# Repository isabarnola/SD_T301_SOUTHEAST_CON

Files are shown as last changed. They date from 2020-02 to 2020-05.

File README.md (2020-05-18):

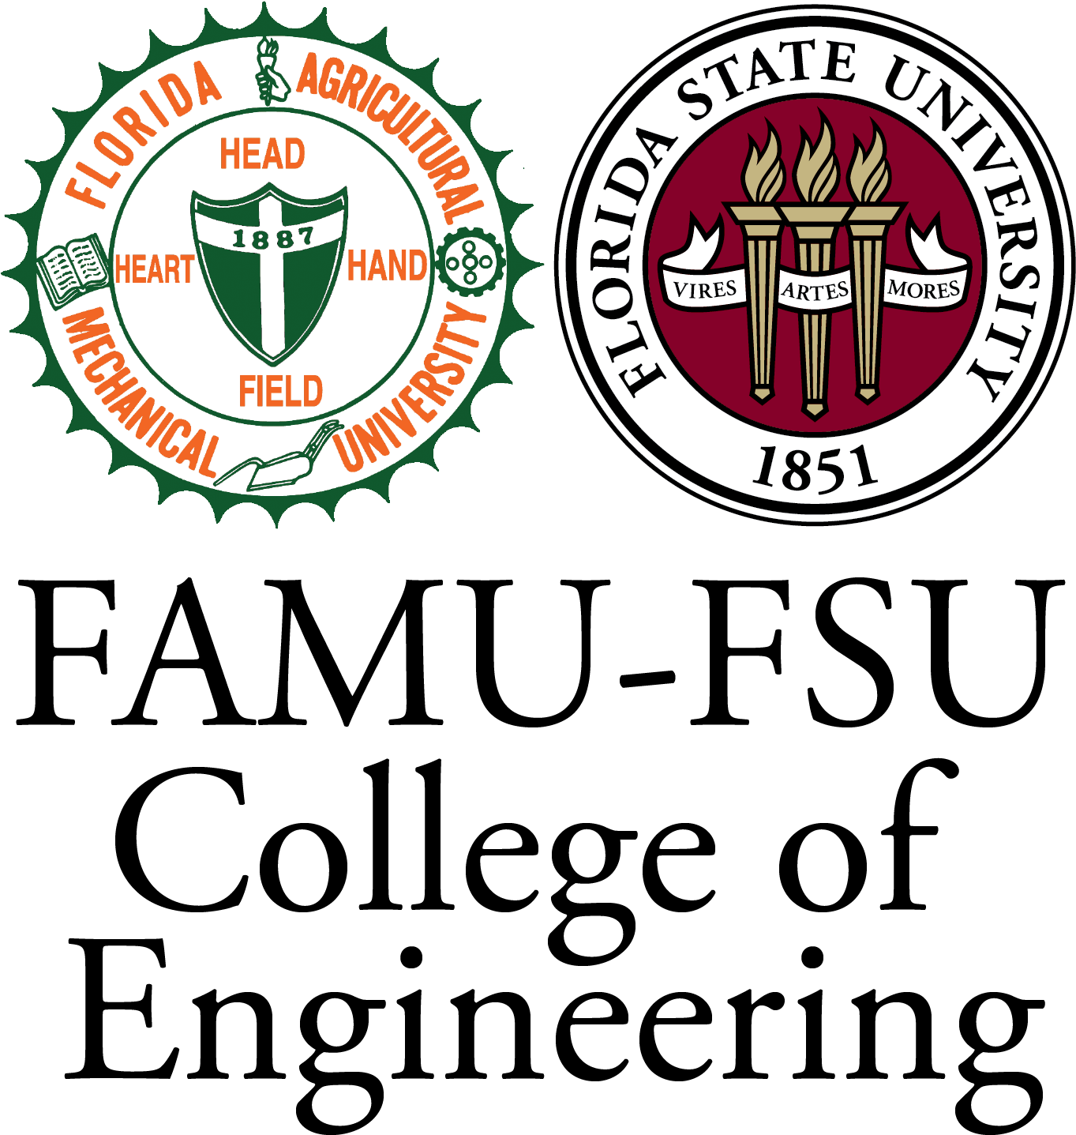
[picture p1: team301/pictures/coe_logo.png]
 

# FAMU-FSU Senior Design Team 301 : SouthEastCon Hardware Competition 

The IEEE SoutheastCon Student Hardware Competition is a yearly robotic design contest. 
This year’s game is to design an autonomous robot to do at least 1 of 2 tasks, within 3 minutes. 

Competition's webpage: 
```
https://attend.ieee.org/southeastcon-2020/student-program/student-hardware-competition/
```
Team's webpage:
```
https://ww2.eng.famu.fsu.edu/me/senior_design/2020/team301/
```
or
```
https://ww2.eng.famu.fsu.edu/~barnois/team301/
```

## 

Here you'll find the code for team 301's automated robot Ezio! As well as all other code related to the project.

### Ezio
Ezio is team 301 response to the souteascon harwarecompetition of 2020 1st challenge. He will stack from the bottom in a reverse PI Order.
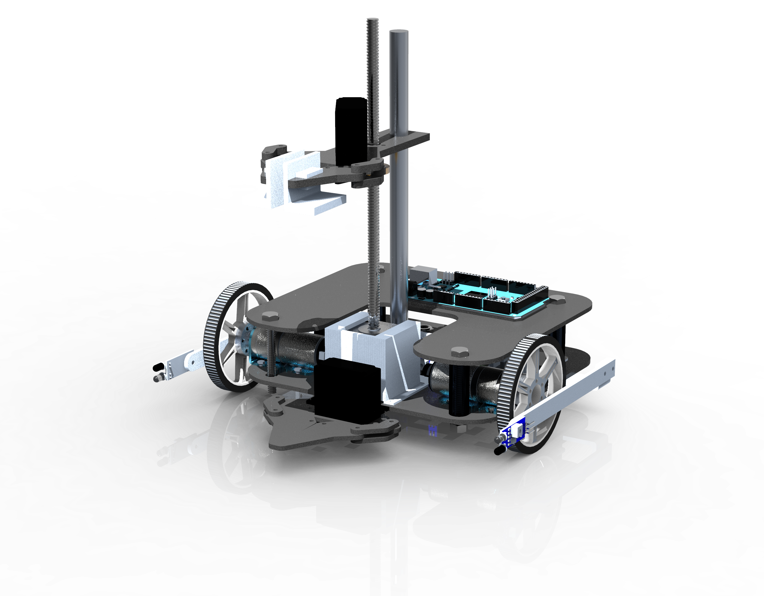
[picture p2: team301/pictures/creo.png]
Ezio


### Prerequisites

What things you need to install the software and how to install them

```
https://www.arduino.cc/en/Main/Software
```

### Software Overview

The software was designed to resemble a Finite State Machine. 
The tasks needed to do by Ezio were separated into modules, or states. 
Depending on the amount of blocks stacked, Ezio will use one state or another
in order to finish the task. Each state contains multiple functions in order 
to modularize the software's implementation. This type of desing allows 
for easier implemenation and testing as the project progresses.

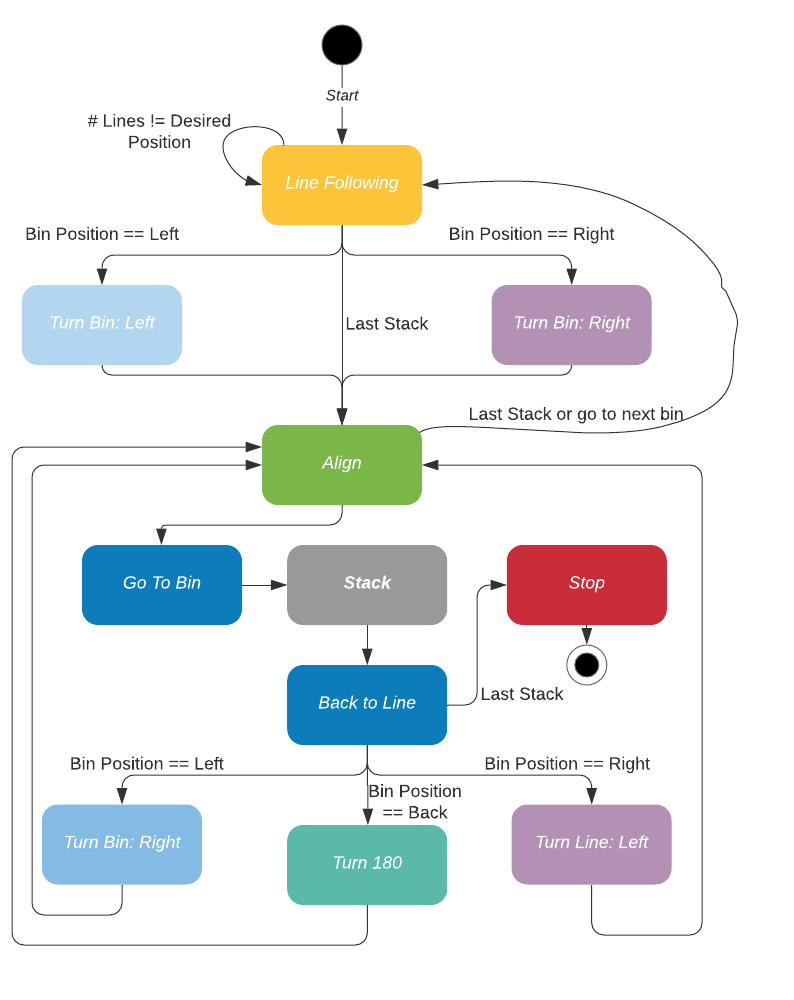
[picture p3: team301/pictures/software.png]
Software Diagram


## Authors

* **Isabel Barnola** - *Initial work* 

## License

No License

## Acknowledgments

* Hat tip to anyone whose code was used
* Inspiration
* etc

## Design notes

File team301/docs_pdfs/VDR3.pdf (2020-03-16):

# IEEE SoutheastCon Student Hardware Competition: Team 301

Isabel Barnola • David Bowen • Diego Campos • Alex Ndekeng • Abiel Souverain

Advisor: Dr. Bruce Harvey • Instructor: Dr. Jerris Hooker
Summary | Design

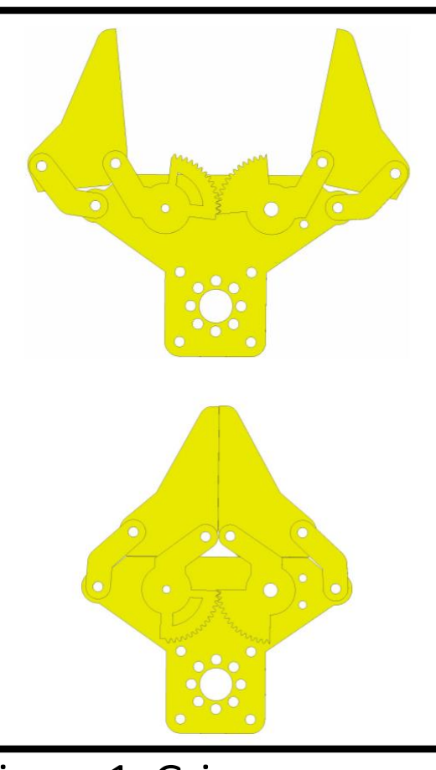
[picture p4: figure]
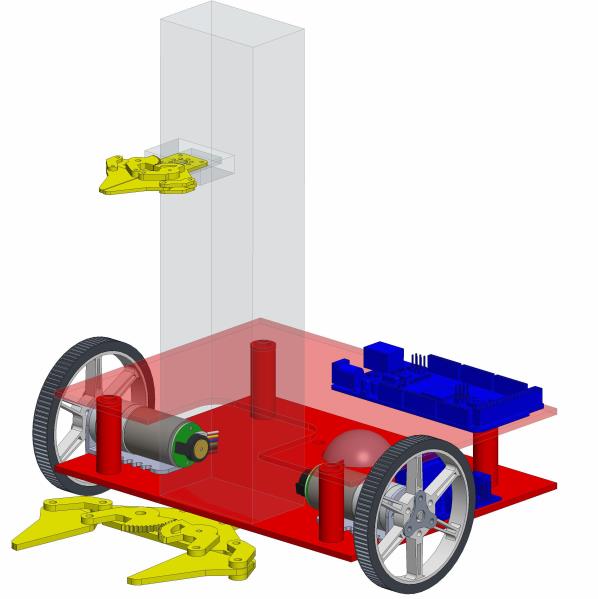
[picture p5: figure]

For the IEEE SoutheastCon 2020 Hardware Competition the goal is to make an automated robot that can complete at least one of the
challenges. Different points are awarded for different tasks, and the objective is to get the most points in 3 minutes.

There are two challenges, to stack Legos and push buttons. Each challenge is given points as shown in the figure below.
- Lego stacking: stack as many Legos in pi order where different colored Legos represent different numbers.
- Button pushing: push as many buttons in pi order where different buttons represent different numbers. Any additional button presses that are out of order will be added to the total, but this number is capped at 100.

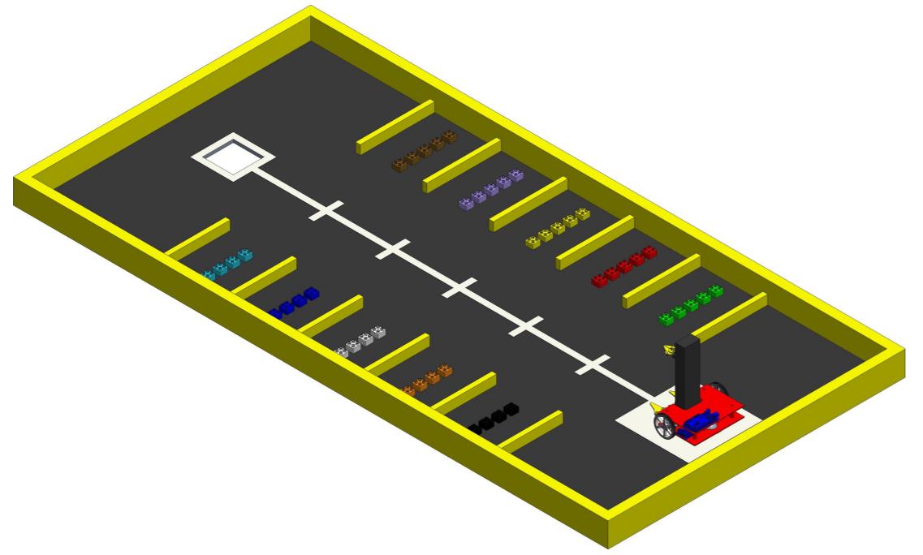
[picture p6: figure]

## Acknowledgements

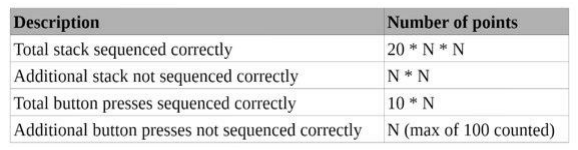
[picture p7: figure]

We thank Dr. Bruce Harvey for overseeing the design process, giving us access to a lab with many components that we will need, and for getting the competition play field built for us. We thank Dr. Hooker, Dr. Chuy, and Dr. McConomy for their constructive criticism in the design phase of our project.

## Challenges

## Future Work

Mechanical Design:
- Assemble prototype for initial testing
- Finalize design and dimensions Software Design:
- Navigational system
- Line following and line counting algorithm
- Stacking
- Elevator and gripper control
Electronic System:
- Assemble electronic components

## Development Tools

Software used:
- Arduino IDE – Microcontroller
- The automated system that governs the robot will be
deployed on an Arduino Mega.
- The system will be coded using C++
- CAD – Design
- Creo was the software used To develop the robot design

Figure 2. Robot Prototype

Figure 3. Robot in play arena

Figure 1. Gripper
opened/ Closed

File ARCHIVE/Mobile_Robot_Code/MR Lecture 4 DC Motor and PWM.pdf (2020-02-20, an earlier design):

## DC Motor and Pulse Width Modulation

Introduction to Mobile Robotics

1

DC Motor

§▪ Direct Current (DC) motor
- Converts electrical energy into rotational mechanical energy
- Earliest form of motor and it is easy to control.
- High torque and good speed controllability
- Typically used in robotic manipulators and mobile robots.
- Considered as torque generator

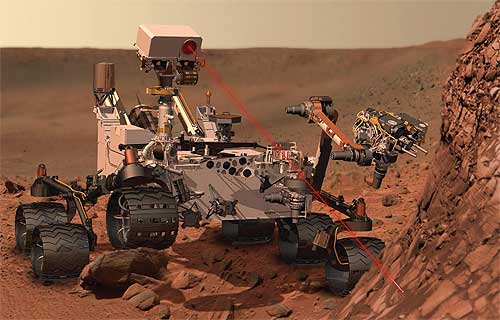
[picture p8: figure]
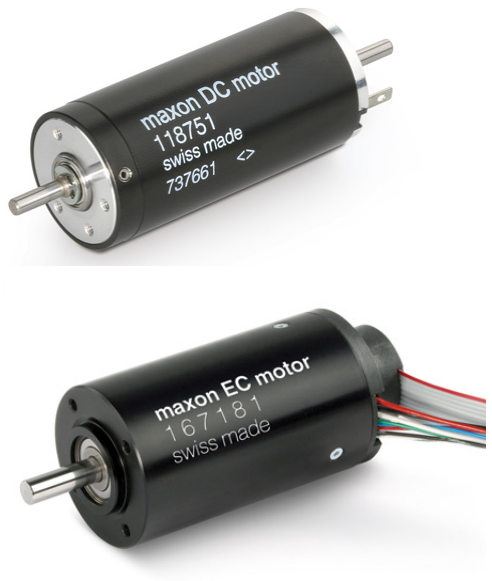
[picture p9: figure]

2

DC Motor

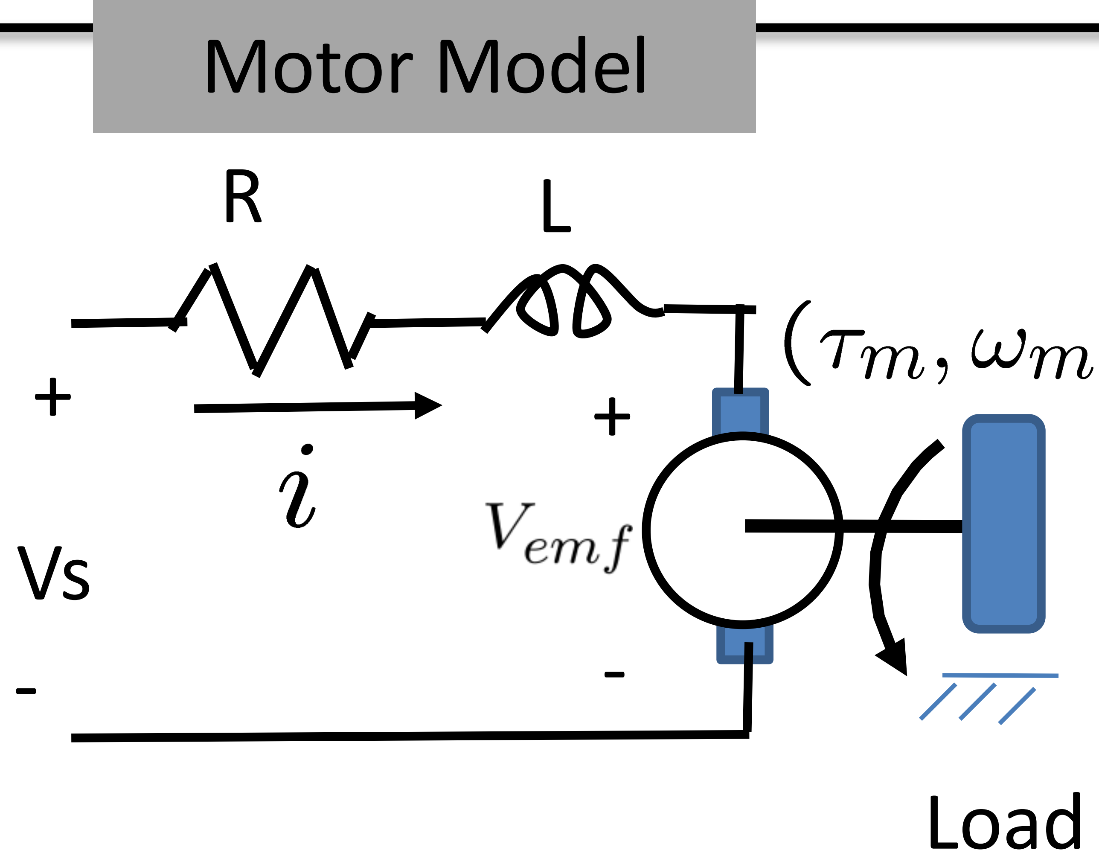
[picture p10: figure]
Load; Motor; Model

§▪ DC Motor Fundamentals
- current flowing through the motor is proportional to the generated torque
- angular rotation generates back-electromotive force
- operation:
- Vs is applied and
current is generated
which translates to
torque generation

3

R

armature

resistance
L

armature

inductance
Kv voltage

constant

V/rpm
Km

torque

constant

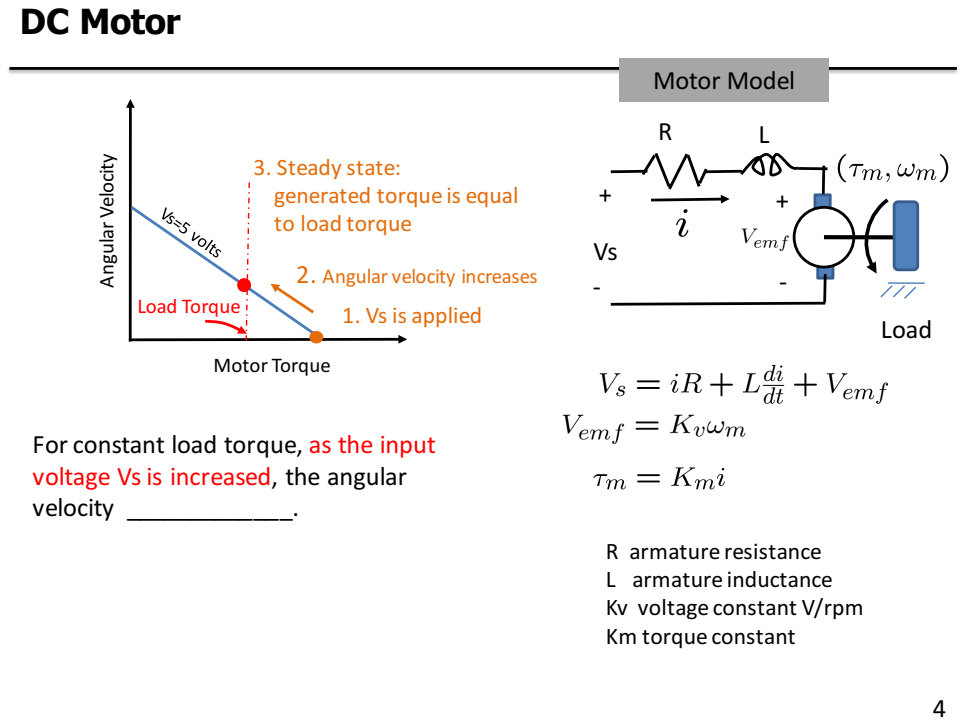
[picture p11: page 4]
DC Motor; Motor; Torque; Angular; Velocity; Load; For; constant; load; torque,; the; input; voltage; increased,; angular; velocity; armature; resistance; inductance; Kv voltage; V/rpm; torque; Model; applied; increases; Steady; state: generated; equal

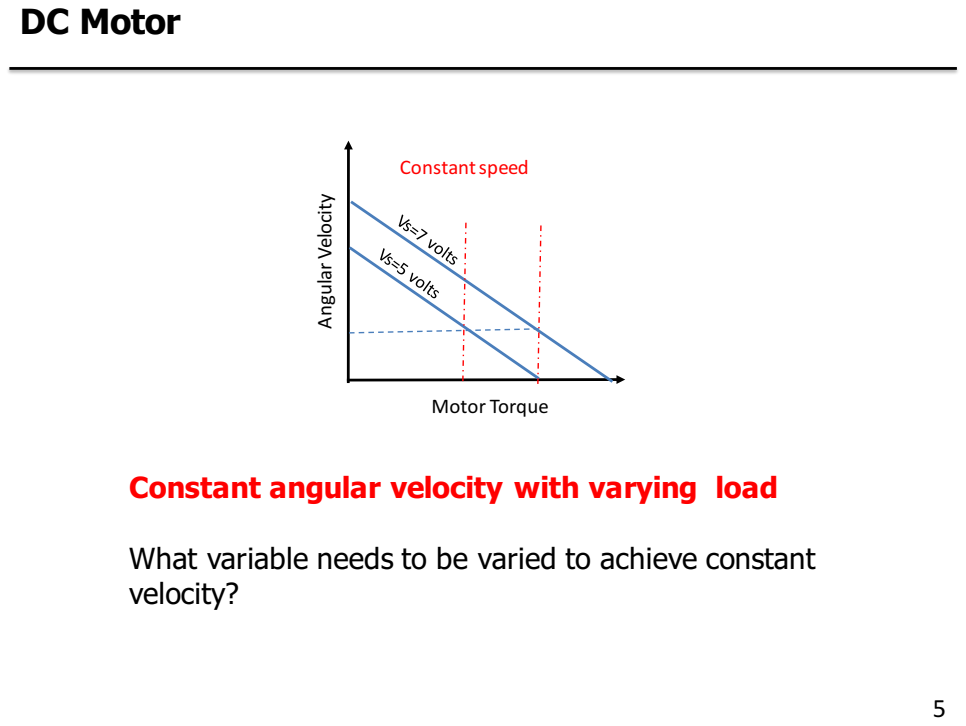
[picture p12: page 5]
DC Motor; Motor; Torque; Angular; Velocity; Constant; speed

Constant angular velocity with varying load

What variable needs to be varied to achieve constant
velocity?

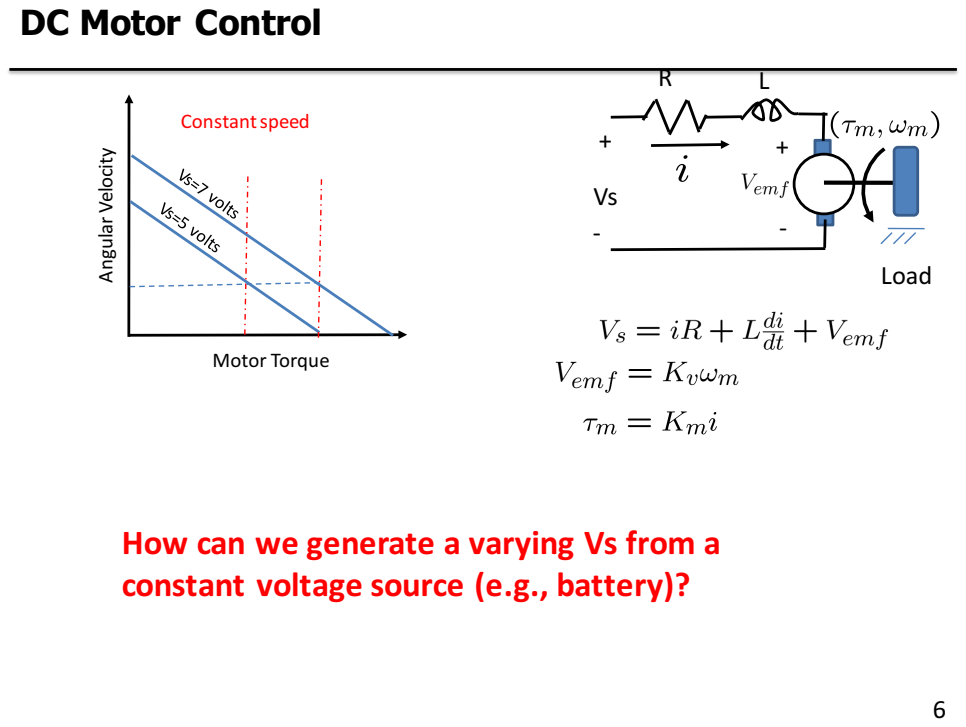
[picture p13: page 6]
Motor; Torque; Angular; Velocity; Constant; speed; Load; How; can; generate; varying; from; constant; voltage; source; battery)?

DC Motor Control

Introduction

§▪ Pulse Width Modulation
- an efficient way of controlling motors
- DC or average value is changed by varying the duty cycle

7

Introduction

§▪ Pulse Width Modulation
- Typical PWM freq. = 1/T is 100 Hz to 10 kHz.

8

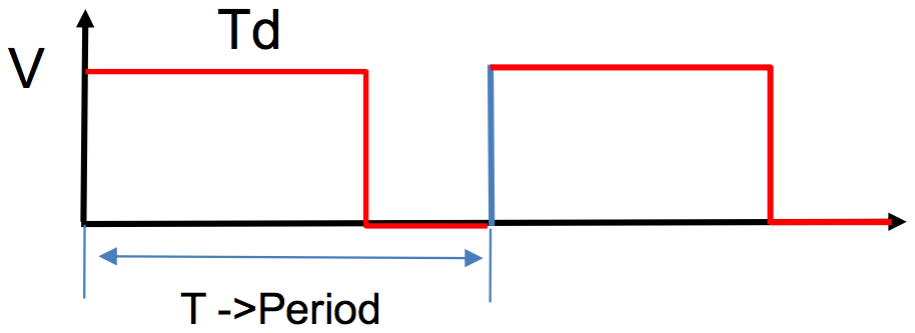
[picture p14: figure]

V"# =

$

% ∫ v(t) %
+ dt

V"# =

$
%

Area

PWM

§▪ Duty Cycle

9

Duty Cycle =

23456 75 8798 (:3;<)
26=7>: | x 100%

Duty Cycle =

?:
?

x 100%

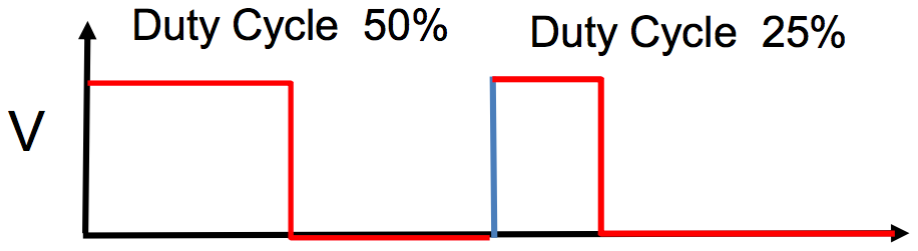
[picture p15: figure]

Pulse Width Modulation

§▪ Draw a PWM signal with 75% duty cycle

10

PWM and Microcontroller Bit Representation

§▪ Computer (Microcontroller)
- Arduino Mega 8 bit microcontroller will be used to control the mobile base

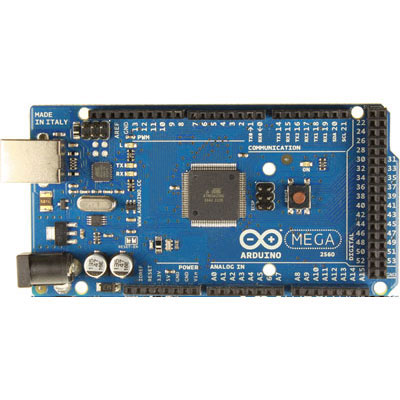
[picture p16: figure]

11

PWM and Microcontroller Bit Representation

§▪ BIT or bit
- smallest memory unit
§▪ N bit system (microcontroller)
- Represents N bit data size, register, data bus, and address bus.
- For example, an 8 bit system implies that the registers are 8 bit. §▪ N bit PWM
- Implies that 0--100% duty cycle is represented by 0 – (2A − 1).
- For example an 8 bit PWM has the mapping below
duty cycle (%)
0 | 0
50 | 127
100 | 255

12

PWM and Bit Representation

§▪ In terms of minimum change of output voltage (output voltage resolution), what does a high number of bits imply?

13

PWM on ATmega2560

§▪ Atmega2560 (Microcontroller)
- Used by Arduino Mega
- Note: Built in Arduino function for PWM has a frequency of 500 Hz, which is intended RC servo motors and other devices. Some applications require different freq. or higher frequency. Hence, we will not use Arduino built in function.

§▪ In the given sample code, PWM generation will be based on TIMER 5
- Pin 45 for motor 0
- Pin 46 for motor 1

14

PWM Implementation Using Arduino Mega

15

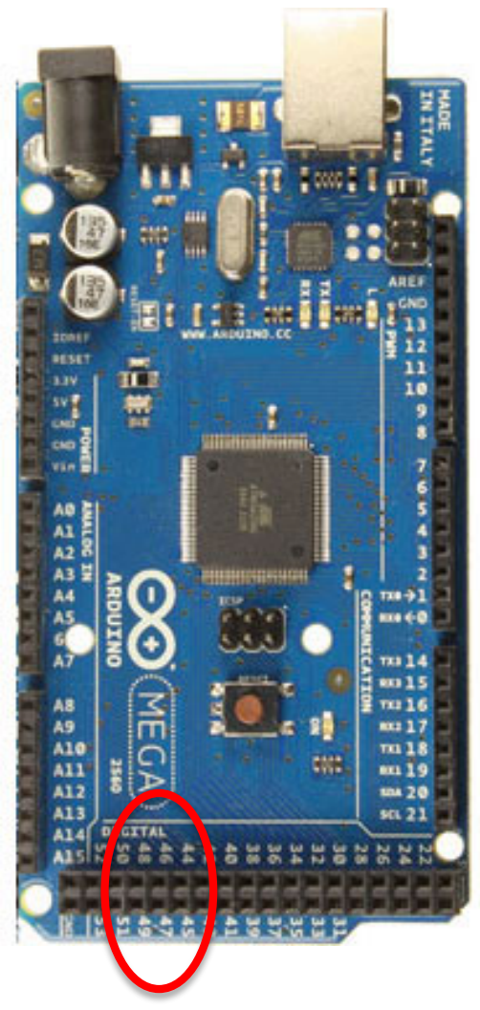
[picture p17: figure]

Code Initialization

16

pwm_init();

void pwm_init(void){
pinMode(45, OUTPUT);
pinMode(46, OUTPUT);
TCCR5A = _BV(COM5A1) | _BV(COM5B1) | _BV(WGM52) |
_BV(WGM50);
TCCR5B = _BV(CS51) | _BV(CS50); //set prescaler to 64
OCR5A = 0; OCR5B = 0;
}
The

above

code

(pwm_init)

initializes

timer

5

as

PWM

generators(2

PWMs).
The

PWMs

are

8

bits

at

500

Hz.

TCCR5A,

TCCR5B,

OCR5A,

and

OCR5B

are

microcontroller

registers

and

already
defined

in

the

ARDUINO

environment.

PWM Duty Cycle

§▪ OCR5A (Output Compare of TIMER 5)
- Will set the duty of channel/motor 0. The maximum value of duty is 255.
255 -> 100% duty cycle 127 -> 50% duty cycle
0 | -> | 0% duty cycle

17

PWM Duty Cycle

18

§▪ OCR5B
- Will set the duty of channel/motor 1. The maximum value of duty is 255.
255 -> 100% duty cycle 127 -> 50% duty cycle
0 | -> | 0% duty cycle

Motor Driver

19

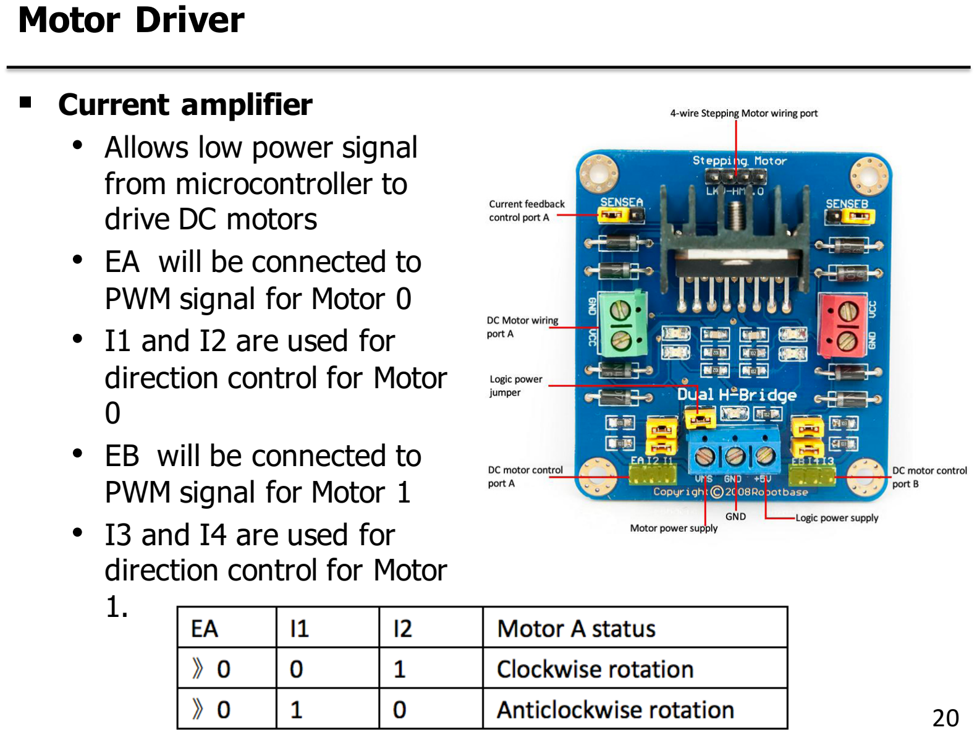
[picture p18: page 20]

Motor Driver §▪ Current amplifier • Allows low power signal

from microcontroller to
drive DC motors
- EA will be connected to PWM signal for Motor 0
- I1 and I2 are used for direction control for Motor 0
- EB will be connected to PWM signal for Motor

1
- I3 and I4 are used for direction control for Motor 1.

20

Motor Driver

§▪ Motor Control Summary
- Aside from PWM signal, a motor needs 2 digital pins for direction.
- For a differentially steered (2 wheels) mobile robot
- 2 motors – 2 PWM signals and 4 direction pins

21

Motor Functions

22

motor_init()

initializes

the

PWM

and

direction

pins

of

the

motors

set_motor_speed(channel,

speed

)
channel

=

0

implies

motor

0

and

channel

=

1

-‐>

motor

1
speed

=

127

implies

50%

duty

cycle

moving

forward
speed

=

-‐127

implies

50%

duty

cycle

moving

backward

void motor_init(void);

void set_motor_duty(int channel, int duty);

Trouble Shooting

set_motor_speed(0,100) should yield a forward motion. If it is backward, you can reverse the motor wiring (+ -> -) or change the direction code.

23

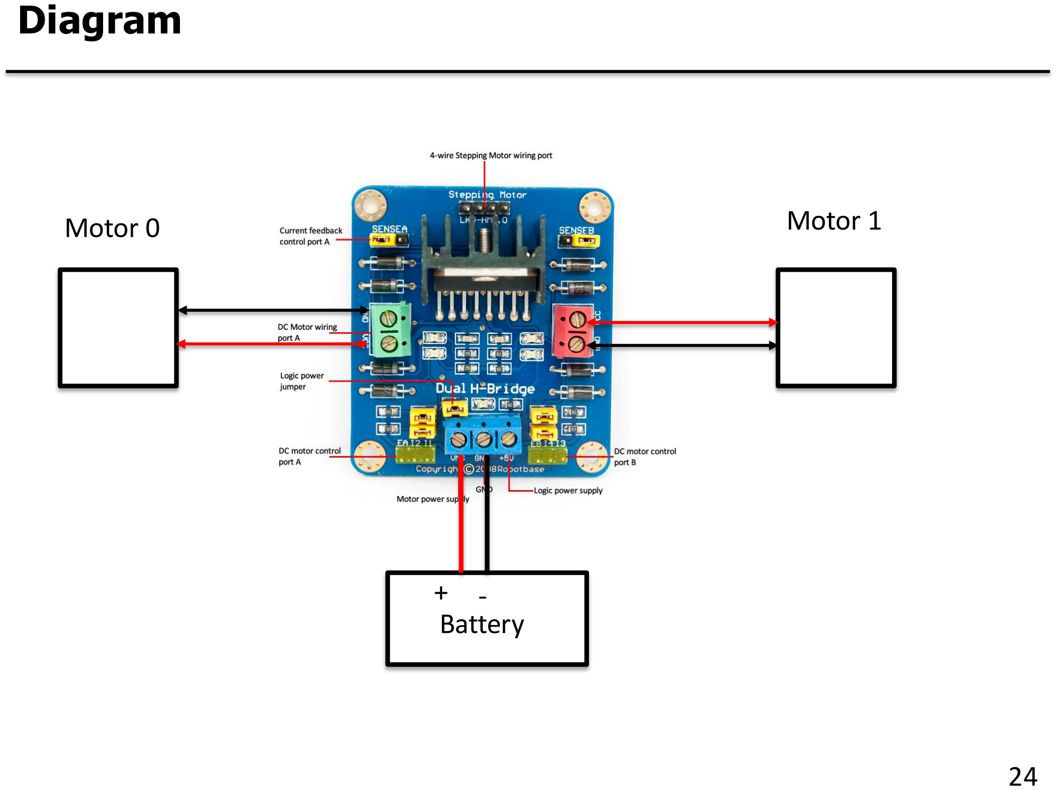
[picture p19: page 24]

Diagram

24

Motor

0 | Motor

1

+ -‐ Battery

Pins

25

Arduino | Motor Driver
45 | EA
50 | I1
51 | I2
46 | EB
52 | I3
53 | I4
GND | GND
+5V | +5V

PWM

PWM

Direction
Direction

Direction
Direction

Sample Code

26

#include "mrobot.h”

void setup()
{
motor_init();
}
void loop() {
set_motor_speed(0,100);
set_motor_speed(1,100);
}

Summary

- The provided motor functions can change the voltage and thereby change the speed of the motor.

- The main drawback is that the implementation is open loop, meaning for a constant duty or voltage, the speed will change if the load varies.

27

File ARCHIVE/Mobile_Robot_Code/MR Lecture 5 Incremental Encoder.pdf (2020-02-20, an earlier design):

## Mobile Robot: Measuring Wheel Position Using Incremental Encoder

1

Introduction

§▪ Incremental Encoder
- Use to measure angular position and generally attached to motor shaft.

2

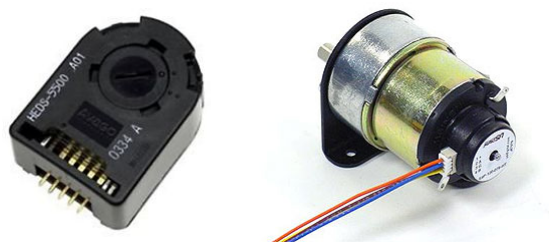
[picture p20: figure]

Introduction

§▪ Incremental Encoder
- Generates two signals that are 90 deg. out of phase

3

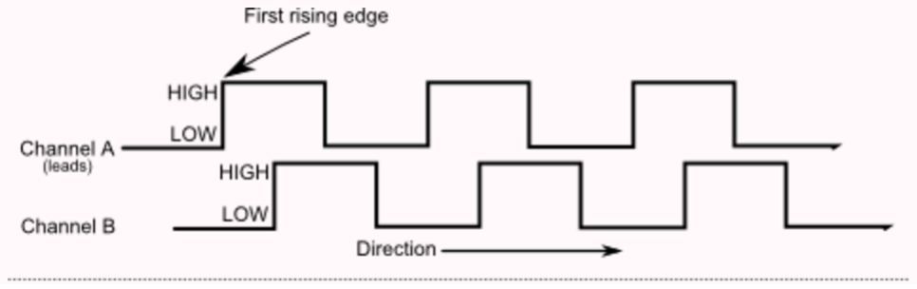
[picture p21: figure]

Introduction

§▪ Decoding Incremental Encoder (Quadrature Decoding)
- Channel A and Channel B will be wired to interrupt pins. If there is a change in state for example high to low or low to high an interrupt is triggered.
- Quadrature decoding – all rising and falling edges create interrupts. Quadrature since there are four sign changes in Ch A and Ch B for one encoder count.

4

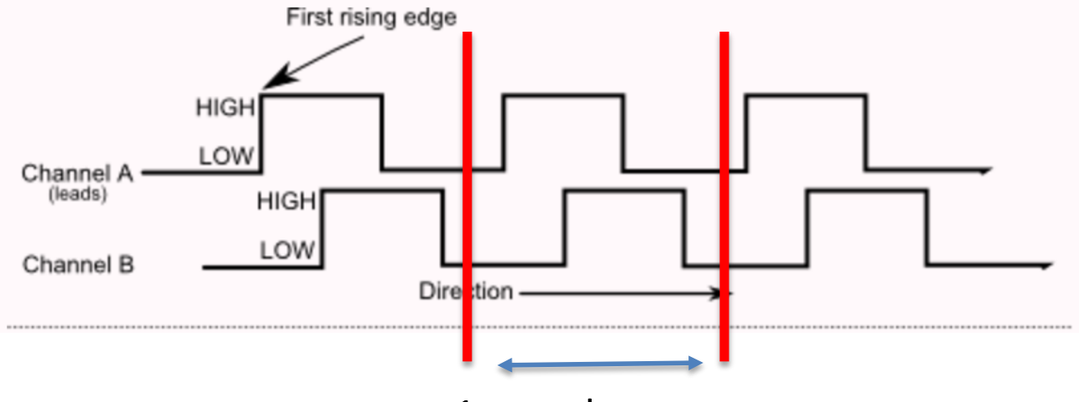
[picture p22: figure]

1

encoder

count

Introduction

§▪ Decoding Incremental Encoder (Quadrature Decoding)
- State assignment – assign states to one count as basis for determining direction.

5

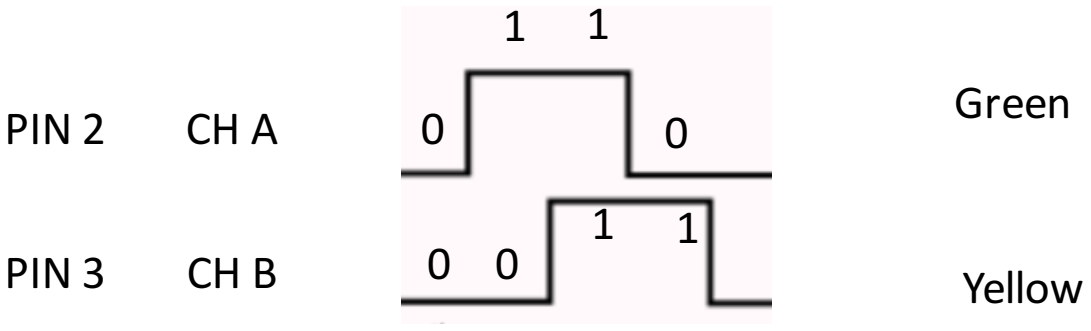
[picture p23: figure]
PIN; Yellow; Green

CHB

CH

A
0
0 | 0
1 | 1 1 | 1 0

State

0 | 1 | 3 | 2

Decoding

§▪ Conditions:
- If current state is 0 and next state is 1 then in clockwise direction (increment the value of the encoder)
- If current state is 0 and next state is 2 then in counter clockwise direction (decrement the value of the encoder)

6

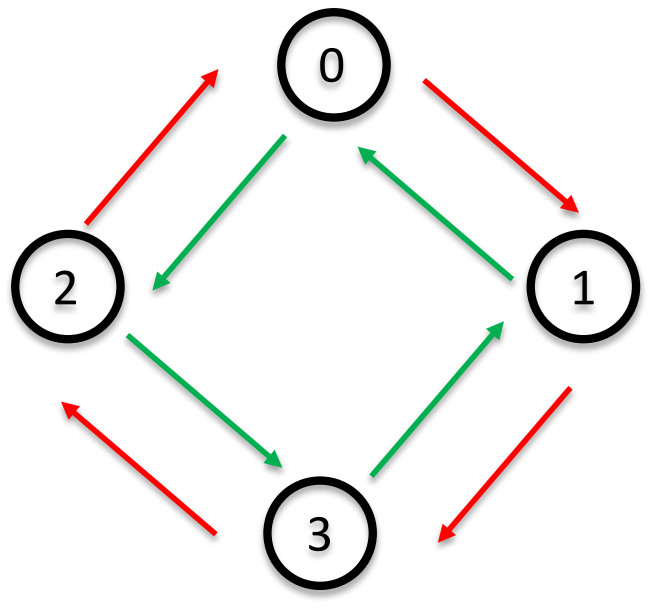
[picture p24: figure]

Encoder

7

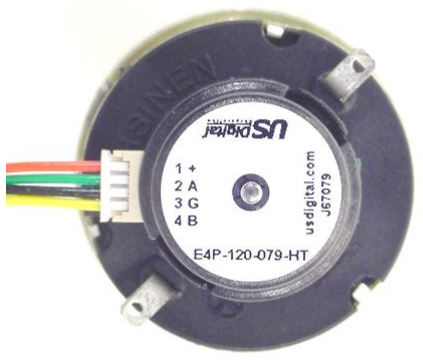
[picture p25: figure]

Red = +5vdc
Black = Ground
Green = Output A
Yellow = Output B

Encoder functions

encoder_init();

Initialize the encoder. Global variable encoder0_val will have the position of motor 0 and encoder1_val will be the position of motor 1.

Note the values of encoder0_val and encoder1_val are in terms of counts. For example, 20000 counts per wheel revolution.

8

Counts

per

wheel

revolution

=

4*

encoder

counts

per

rev

*

motor

gear

ratio

Wheel

Position

(radians)

=

encoder_val /

(counts

per

wheel

revolution)

Test Code

#include "mrobot.h”

void setup()
{ encoder_init();
serial.begin(9600);
}

void loop()
{
Serial.println(encoder0_val); //Serial.println(encoder1_val); }

9

Encoder

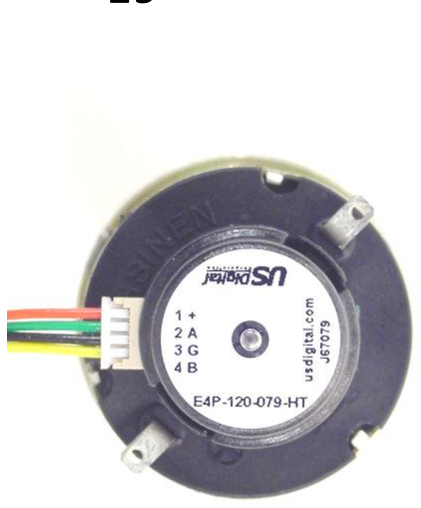
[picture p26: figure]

10

Arduino

Pins | Encoder

2
3
| Encoder
| 0 CHA

18

| Encoder
| 0 CHB

19

| Encoder
| 1 CHA Encoder
| 1 CHB

Note

| encoders have

+5

and

GND

pins.

Left

Wheel

Right

Wheel

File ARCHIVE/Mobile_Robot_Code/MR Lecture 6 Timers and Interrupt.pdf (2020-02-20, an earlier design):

## Real-time Interrupt (Timer)

1

### Timer

§▪ Timer (Realtime Interrupt)
- Creates a deterministic execution of a function
- For example, use to numerically determine velocity from position information (encoder)

2

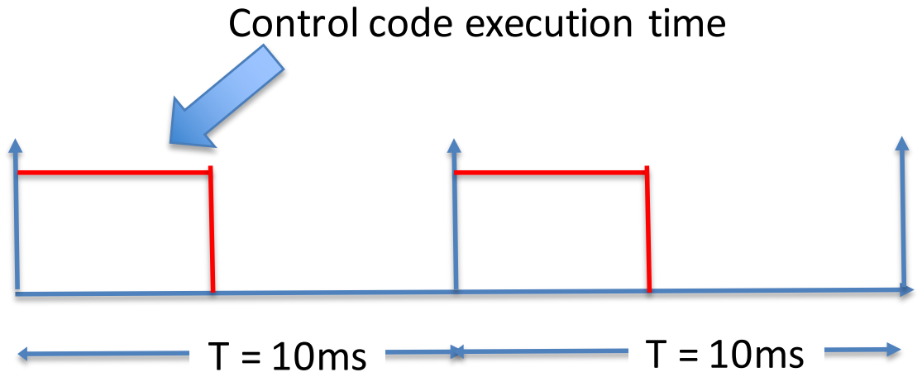
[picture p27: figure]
Control; code; execution; time

### Timer

§▪ Deterministic function execution
- Allows to accurately determine time derivative of a signal for example velocity

3

velocity | n | = (position | n | − position | n − 1 | )/T

Current

velocity

| | = (current

position

– previous

position)/T

### Timer Implementation (Timer1)

void setup_timer(void);

The function setup_timer() creates an interrupt every 10ms and execute ISR(TIMER1_COMPA_vect)

/*The function below is coupled to timer1 interrupt*/

ISR(TIMER1_COMPA_vect)
// timer compare interrupt service routine {
control();
}

4

### Additional Functions for Mobile Robot Control (mrobot.h)

5

### Additional Functions that are executed every 10ms

void get_current_status(void);

The above function determines the current velocity of the wheels.

void low_level_control(void)

Computes the desired voltage and duty to track the desired velocity.

6

voltage = K7 desired position − current position + K<(desired velocity − current velocity)

### Low Level Control

§▪ Based on PD (Proportional + Derivative) Control

§▪ Given Vcc and for a 8 bit PWM, what is the expression for duty?

7

voltage = K7 desired position − current position + K<(desired velocity − current velocity)

duty

=

### Sample Code

#include "mrobot.h”

void setup() {
setup_timer();

/*This will setup an Interrupt Service Routine to be executed at 10ms*/

encoder_init();
motor_init();
Serial.begin(9600);
}
void loop() {

}

8

### Sample Code

void control(void){
get_current_status();
/******************************/
des_wvel[0] = 0.25; // set motor 0 to 0.25 rad/sec des_wvel[1] = 0.25; // set motor 1 to 0.25 rad/sec /********************************/ low_level_control();
}
/**This function will be executed every 10ms **/ ISR(TIMER1_COMPA_vect) /* timer compare interrupt service routine*/
{
control();
}

9

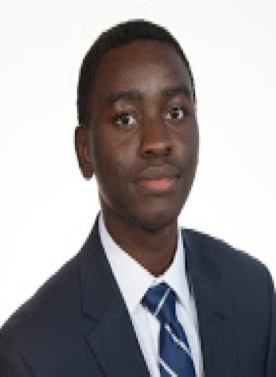
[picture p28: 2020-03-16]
team301/pictures/AN.png

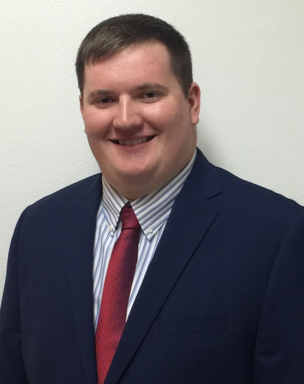
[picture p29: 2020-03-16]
team301/pictures/DB.png

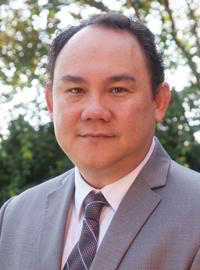
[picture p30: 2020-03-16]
team301/pictures/Oscar-Chuy.png

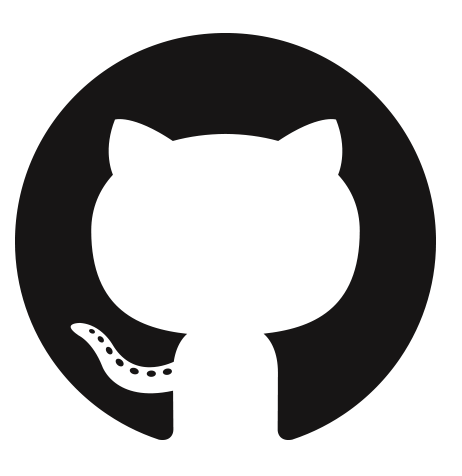
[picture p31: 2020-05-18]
team301/pictures/g.png

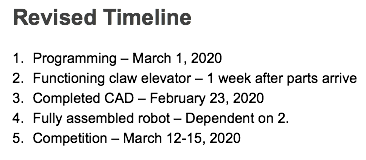
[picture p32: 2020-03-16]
team301/pictures/timeline.png

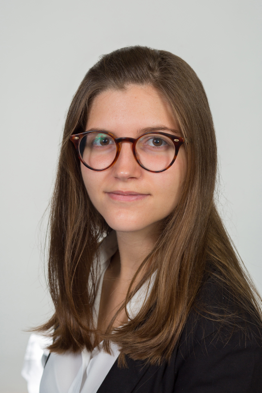
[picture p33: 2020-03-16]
team301/pictures/IB.png

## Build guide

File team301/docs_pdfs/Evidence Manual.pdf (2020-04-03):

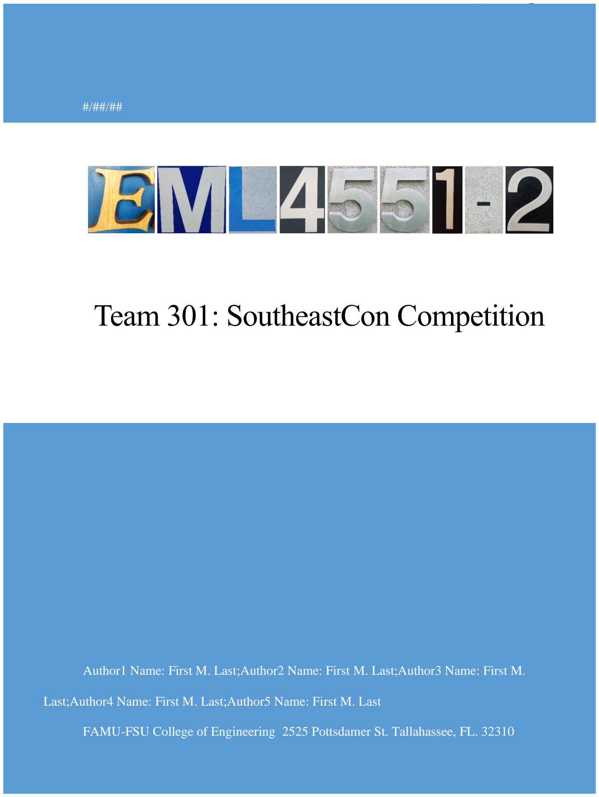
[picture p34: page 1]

Team 301 | i

Author1 Name: First M. Last;Author2 Name: First M. Last;Author3 Name: First M.

Last;Author4 Name: First M. Last;Author5 Name: First M. Last

FAMU-FSU College of Engineering 2525 Pottsdamer St. Tallahassee, FL. 32310

# Team 301: SoutheastCon Competition

#/##/##

Team 301 | ii

Abstract

The IEEE SoutheastCon Student Hardware Competition is a yearly robotic design contest. This

year’s game is to design a robot, that drives itself, to do 1 of 2 things or both, within a 3-minute

time limit. The 1st game is to use 10 push buttons that are along one of the walls of the field to

type out as many digits (0-9) of the number PI (3.14159...) as possible. The 2nd game is to stack

Lego Duplo blocks of different colors in order, within the scoring area. There are 10 different

block colors and each color represents a different digit (0-9). The goal is to stack as many blocks

as possible in the order of PI.

Our robot follows a planned route to gather the Duplo blocks and stacks them as it goes around

the field. Toward the end of the 3-minute time limit, the robot moves over to the goal to place the

stack of Duplo blocks. The robot carries the Duplo blocks by having two claws, one on the

bottom and one on the top. The claw at the bottom lines up the Duplo blocks so the top claw can

pick it up with no problems. Then the top claw moves up and holds the Duplo block in place so it

can stack with the new incoming Duplo block.

Keywords: list 3 to 5 keywords that describe your project.

Team 301 | iii

Disclaimer

Your sponsor may require a disclaimer on the report. Especially if it is a government sponsored project or confidential project. If a disclaimer is not required delete this section.

Team 301 | iv

Acknowledgement

These remarks thanks those that helped you complete your senior design project. Especially those who have sponsored the project, provided mentorship advice, and materials. 4

- Paragraph 1 thank sponsor!
- Paragraph 2 thank advisors.
- Paragraph 3 thank those that provided you materials and resources.
- Paragraph 4 thank anyone else who helped you.

Team 301 | v

Table of Contents

Team 301 | vi

Team 301 | vii

Team 301 | viii

List of Tables

Table 1. Customer Rank Order | 5
Table 2. Pugh Matrix 1 | 22
Table 3. Pugh Matrix 2 | 23
Table 4. Final AHP Matrix | 25
Table 5. Criteria Weights | 25
Table 6. Concept and Alternative Value | 25
Table 7. Cross-Reference Table | 40
Table 8. Functions, Metrics, and Targets | 41
Table 9. Morphological Chart | 45

Team 301 | ix

List of Figures

Team 301 | x

Notation

Team 301 | 1

Chapter One: EML 4551C

### 1.1 Project Scope

Project Brief

We will be competing in the 2020 Southeast Con hardware competition. The competition

will consist of 2 sub-competitions. The goal of the first challenge in the competition is to

accurately stack Lego Duplo blocks representing the digits of pi. Each digit from 0 – 9 is given a

color representation (e.g. 3 is represented by an orange block). The goal of the second challenge

is to push buttons in an order that represents the digits of pi. Both challenges must be completed

by a completely autonomous device that fits into a 1 ft3 space. Other robots, such as the robot

showcased in the video by TKJ electronics, can recognize the color of and stack Duplo blocks,

but it is not mobile, nor does it fit into the required volume (Electronics, 2017).

Description

The product will be an autonomous robot with the capabilities of completing at least one

of the two challenges set for the 2020 SoutheastCon hardware competition.

Key Goals

The main goal of this project is to build an autonomous robot, or robots, that meet the

specifications and can score as many points as possible. Another key goal is that the robot can

score by pushing the buttons in the correct order, or stack 2x2 Duplo colored bricks in the correct

sequence. Lastly the robot(s) can traverse the playing field.

Primary and Secondary Markets

Team 301 | 2

The primary market will be the judges at the competition, where our product will

compete. The secondary market will include potential future employers, and other schools who

will see our robot competing.

Stakeholders

The primary investor for this project is our sponsor, the FAMU-FSU College of

Engineering. Our professors, Dr. Hooker and Dr. McConomy are also stakeholders in the project,

as they will be providing our final grade. Dr. Harvey, our academic adviser, will provide us with

valuable knowledge from past experiences with the project.

Assumptions

We must assume that the measurements as well as the rules given to us in the rules will

be accurate so we can build a robot that works for those specifications. We are assuming that the

Duplo blocks that we purchase (for practice) will be the same as those used in the competition.

We will also assume a certain brightness of lighting so that cameras to be able to accurately see

the buttons or Legos.

### 1.2 Customer Needs

Because of the nature of the project, it was difficult to define who the customers were.

The conclusion was that our stakeholders, those invested in our project, and the rules given to us

would be our primary source of customer needs. We have also planned to communicate with

those in charge of the competition for clarification of rules and guidelines. The judges in the

competition may also be a potential customer, but given the time constraints, their responses

could not be currently included.

Rules Breakdown

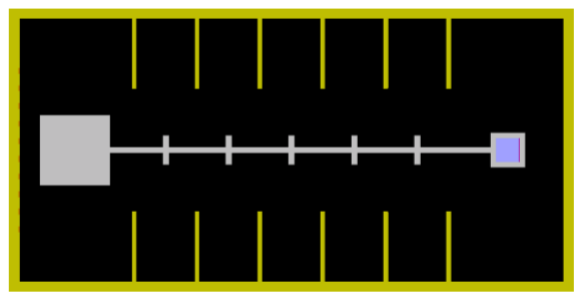
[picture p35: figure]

Team 301 | 3

The goal of the IEEE SoutheastCon 2020 Hardware competition is to design a robot that

stacks a series of Lego Duplo blocks, and/or inputs as many digits on a set of 10 pushbuttons in a

three-minute competition. These challenges will take place in an arena like the one depicted on

fig 1.

Figure 1. IEEE SoutheastCon 2020 Hardware Competition Arena (Radford, 2019)

Robot: Is completely autonomous and fits entirely within a 12”x12”x12” cube at start of match.

The robot is required to stay within the arena. The robot may expand beyond initial size and

may be split in several robots. Independent robots ought to communicate with each other over a

wired link. A clear and visible labeled start switch is required for all robots. The robot cannot

contain any explosives, pyrotechnic, toxic or corrosive materials, or flammable liquid gases. The

robot cannot pose any danger to the arena, judges or spectators. Flying robots are not allowed.

Challenges:

Stacking Pi Digits: Stack as many digits of Pi within the competition match time. Points are

awarded by total height of stack and how many digits of pi are in the correct order, starting from

bottom to top. A different Lego Duplo block will represent a different digit using the following

protocol:

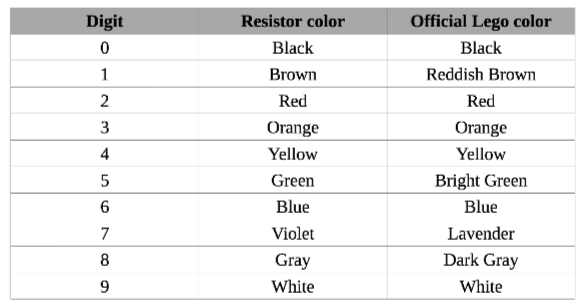
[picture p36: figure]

Team 301 | 4

Figure 2. Standard Resistor-Lego Block (Radford, 2019)

The Lego blocks must be stacked within a 5”x5” hole at the opposite the robot’s starting

position. Each team may provide a base. If base is provided in advance, it may not contain

motors, LEDs, processor, beacons or switches. Teams are responsible for stocking the ten bins

with 10 blocks. Lego blocks may be arranged in any fashion inside the bins, however only on

Lego block color is allowed per bin. A maximum of 15 blocks of each color is available per

team.

The score will be based on the height of the stack after the end of the match. The robot

needs to release the stack once the time of the match finishes. If more than one stack exists, the

highest one will be used.

Pressing Buttons: Enter as many digits of Pi on the 10 pushbuttons within competition

time. Points are awarded by total number of buttons presses as well as how many digits of pi are

entered in the correct order. At start of competition, pushbutton 3 will illuminate, and then

number 1, and so on in the order of digits of Pi. Each button must be pressed for at least 50 ms,

and between each button press at least 100 ms should pass. Teams will receive smaller points for

any button presses after the last valid button press.

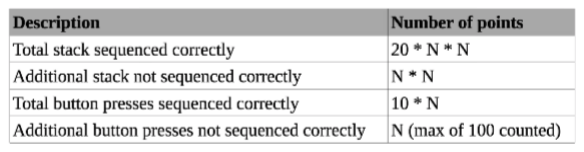
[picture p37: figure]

Team 301 | 5

Competition: The competition will consist of two preliminary runs. The top four highest

scoring teams in preliminary runs will then compete in final run. The final round will only

consider points scored in that final round. Each match will last for a maximum of 3 minutes.

Scoring: The points awarded by category are depicted in the following figure:

Figure 3. Points Awarded Per Category (Radford, 2019)

Survey Responses

In order to further define our customer needs, a survey was sent to our professors and

adviser. Dr. Bruce Harvey emphasized the avoidance of 3D printing as a source of manufactured

parts, as another team did in the past. Dr. McConomy’s response was to be perfect, as the

success of the product heavily relies on the robot(s)’ accuracy. One of the questions asked in the

survey was to rank possible functions of the robot. Dr. Harvey’s and Dr. Hooker’s responses to

the question can be found in Table 1.

Customer Rank Order below.

Dr. Hooker, prior to completing the survey, advised that we perform to the best of our

ability. He emphasized the importance of planning to avoid redesigns in the future.

Table 1.
Customer Rank Order

Team 301 | 6
| Dr. Harvey | Dr. Hooker
Mobility | 1 | 6
Accurate Stacking | 4 | 1
Accurate Button Pushing | 5 | 2
Stacking | 2 | 3
Button Pushing | 3 | 4
Color Recognition | 8 | 5
Speed | 7 | 7
Automatic Shutdown | 6 | 8

From the responses in Table 1, one of the more important customer needs is that the

product can stack the Duplo blocks. Something important to note is that the rules were updated

and the way the points are scored has drastically changed. Even though in the survey responses

button pushing buttons tops the priority list along with mobility, the rule change has drastically

reduced the points we get from pushing buttons so we will have to put a lot less weight into it.

Regardless of this, seeing the responses from our advisors has helped us get a sense of what is

expected of us so we can have a more guided and informed approach as to what to prioritize in

the robot.

### 1.3 Functional Decomposition

Functional Decomposition is used to break down a system into smaller parts. Often, the

system can be complex, and in order to approach the solution with ease, it is necessary to pull the

system apart. In the cross-reference table below, the Robot is broken down into its main

functions. Through the flow chart depicted in Figure 15, the major functions were then broken

down into minor functions.

Team 301 | 7

After collecting data from the survey and speaking with our advisors, the customer needs

gathered were converted into functions and placed into both a function hierarchy chart and a

cross reference table.

Connection to Systems

The most important system in our product, according to the cross-reference table is the

navigation system. The navigation system plays a role in all the functions required for a

successful product. The recognition system follows the navigation system in order of importance.

The least important system was the push system, because it provides little reward and only

applies to one function. All of the different components that will make up the systems,

mechanical, software, and electrical, will be intertwined, so no component is more important

than the other. The mechanical system will play the largest role in the stacking mechanism.

For the power source for the robot we will be using a battery with enough power to

supply every component in the robot and a factor of safety to prevent overloading.

We will choose what sensors to use depending on what task we choose to have our robot

do:

Lego Stacking:

- Color sensor: senses the color of the Lego blocks
- Sonar sensor: to be able to tell where we are in the field and where the

obstacles/Legos/stacking place is

Button Pushing:

- Light sensor: being able to tell what buttons are lit so we can press them in order
- Would also require a sonar sensor to move and see where the buttons are

Team 301 | 8

The software will interrelate all the before mentioned points, as it will govern the

following modules:

- Pushing Buttons: This module will control lighting sensors and mechanical equipment

which will push the buttons.

- Stack: This module will control sonar sensors, to verify closeness to Legos, and

mechanical component used to stack Legos.

- Navigation: This module will control sonar sensors, motor, and steering.

The “push” system is the least important system, because it is only involved in the button

pushing mechanism. In the design of the product, the system may be removed altogether, if there

are conflicts in the design. The “navigation” system involves the driving of the product around

the field, as well as finding the blocks in the bins and avoiding barriers or other obstacles.

Action and Outcome

The goal of the IEEE SoutheastCon 2020 Hardware competition is to design a robot that

stacks a series of Lego Duplo blocks, and/or inputs as many digits on a set of 10 pushbuttons in a

three-minute competition. This product will be a robot that has all the characteristics necessary

to do the challenges of the competition.

### 1.4 Target Summary

When assessing what our robot could do it is important to consider the best-case scenario

as well as the worst-case scenario to have a ballpark estimate of where we could be placing.

Considering the bare minimum, we would want our robot to do we can divide it into two

Team 301 | 9

categories, a Lego stacking robot and a button pressing robot. For the robot pressing button the

bare minimum we would want is a robot that can push one button once every second even if the

button is not in the order of pi. However, the rules limit incorrect button presses to 100 so the

robot should be able to score 100 points in the competition. If that is what is expected of our

robot then it should be able to move to from the starting position to the buttons in less than 20

seconds, it should then align itself with one of the buttons in less than 10 seconds, and after that

it should press the same button once every second to leave breathing room for the 150 ms

required between button pushes(50ms length of button being pushed and 100ms between

pushes). Now considering the minimum required for the Lego stacking robot we would want it to

score at least as many points as the push button robot so we would set the minimum at 100

points. The best way to achieve this would be by stacking 15 blocks out of order. We could do

this by having 15 Legos of the same color already stacked before the competition began and just

having the robot pick it up and take it to the designated drop off area. To do this we would need a

robot tall enough to be able to carry the stack of 15 Legos. The robot would also be able to drop

it off carefully as to not have the stack topple over. Since it would have 3 minutes to complete

this task the speed it does it at would not be super important, the most important thing would be

to have it do it effectively as in that it can pick up the whole stack and move with it without

disturbing it. Now considering the maximum attainable goals lets again start with push buttons.

For the push buttons we would need to press the buttons of pi in the correct order as quickly as

possible. Assuming that the average time it would take the robot to move from one button to

another would be 1 second and if the robot has to move, we can neglect the 100 milliseconds

between button pushes and just account for the 50 milliseconds required to push the button. This

Team 301 | 10

would give us a time of 1.05 seconds between button pushes and given that we have 180 seconds

and assuming it takes us 5 seconds to go from the starting point to the buttons and subtracting 10

percent since this ideal case will never happen we get 150 button presses in correct order. With

this we would get 1500 points from the button pressing. Now considering the best-case scenario

for the Lego stacking robot we would have the robot stack as many Legos as it could in the

correct order. Assuming we have the base placed before time began and also assuming that it

takes the robot an average time of 5 seconds to go from the Lego bins to the drop off station and

it takes it an average of 2 seconds to stack the Legos as well as an average time of 5 seconds to

go from the drop off station to the correct Lego bin we are looking at an average time of 12

seconds between stacking blocks. Considering we have 180 seconds this means that we would be

able to stack 15 blocks in correct order in this time. However once again taking away 10 percent

from it we would get roughly 13 blocks in correct order which would give us 3380 points. This

robot would need to be mobile since it is very time sensitive and it should be able to correctly

identify where the correct Legos are either with color recognition or hard coding the locations of

the Legos of each color. It should also be able to stack Legos at a height of around 13 blocks.

Considering this information, we can get a rough estimate of how many points we can get and set

realistic goals for ourselves.

Method of Validation

The mission critical functions include to navigate the playfield, recognize where the

Duplo blocks are at, pick the Duplo blocks and stack them correctly at the base. For this project a

replica arena or playfield will be built at the FAMU-FSU college of engineering, and a set of

identical Duplo blocks will be purchased. Using these before mentioned elements, several tests

Team 301 | 11

will be made in order to assess the successfulness of the design. Once the robot is built, it will be

tested on the arena for:

Navigation: The robot will need to pass successfully different checks such as navigating

correctly to the base, and to each of the bins. These will be done by selecting different path

combinations to the bins and base. For example, one of the possible combinations could be, the

robot starts at initial position and then will first go to bin numbered 1, to number 3, and finally to

the base. To deem the navigation effective, the robot must do at least 10 consecutive different

path combinations without a problem.

Recognition: A set of tests will be made to check that the robot effectively recognizes

where the Duplo blocks are. For this the robot will be assigned to go to a bin having Duplo

blocks and will need to stop once it encounters blocks at a “pick up” distance. To ensure the

recognition works correctly the robot will need to pass 10 consecutive tests without a problem,

these tests will be done on random bins and the placement of the Duplo blocks will be aleatory.

Pick up: A set of tests will be made to check that the robot effectively picks up the Duplo

Blocks. The robot will have several blocks laying at a “pick up” distance and it will need to pick

them up successfully, this implies that the robot must pick up the blocks and not let them go

unless specified. For these tests the blocks will be in two combinations, alone or as stacked

towers. To deem the pickup efficacious the robot will need to pass 10 consecutive tests without a

problem.

Stacking: A set of tests will be made to check that the robot effectively stacks the Duplo

Blocks. The robot will already have block or blocks which have already been picked up and will

Team 301 | 12

need to stack these effectively at the base. To deem the stacking efficacious the robot will need

to pass 10 consecutive tests without a problem.

Discussion of Measurements

Most of the measurements will be measured using sensors, so the received voltage will

need to be converted to the metric used for each function. The “navigate the play field” function

is broad and may require some additional metrics to fully define it. Our team may also use the

painted lines in the arena to assist in the navigation from bin to bin, which would require

additional sensors. The navigation can be measured with ultrasonic, photoelectric, or infrared

sensors as well as predefined paths in the software. The “avoid barriers” function will probably

use the same sensors as the “navigate the play field” function. The main objective of this

function is to prevent the robot’s collision with the borders of the playing field. This function

will be measured by the distance from the closest barrier. Both the “Differentiate between

buttons” and the “Differentiate between blocks” functions are measured by the time to reach the

appropriate location. They will still need additional measurements to verify the location. The

correct button, for instance, will illuminate so the robot may need an additional sensor to identify

the correct button. Lifting and lowering the block will be measured by the height difference

between the current block and the previous block placed. This will potentially be measured

through calculating the movements internally, rather than an outside reference.

Summary

The final design selected must achieve all the targets listed in Table 9 below. The metric

and target for the navigate the play field function was deemed critical because the “navigate”

function is the most important function for our product. The other functions are still necessary

Team 301 | 13

for complete success, but without navigation, no points can be scored. If another function, such

as finding the blocks, were to fail points could still be attained through pushing buttons. The

motion of the robots is a function not explicitly listed in the targets and metrics, but falls under

the navigate system.

### 1.5 Concept Generation

The morphological chart was used to generate fifty of the one hundred possible solutions

to the problem Other methods, such as biomimicry and the “anti-problem” were used to generate

the other fifty concepts. The primary methods used were individual brainstorming, group

brainstorming, and biomimicry.

Concept 1.

The robot has a sorter on its body with blocks that slide in. The robot will first grab the block

using an elevator and claw. A gate opens releasing the next color necessary in the stacking

sequence. The robot will sit on 4-wheels and will be rear wheel drive. The two wheels in the

front will be used for steering, guided by a servo motor. Once the gate opens, the block will

slide to a point at which the arm can lift and place it in the correct stack.

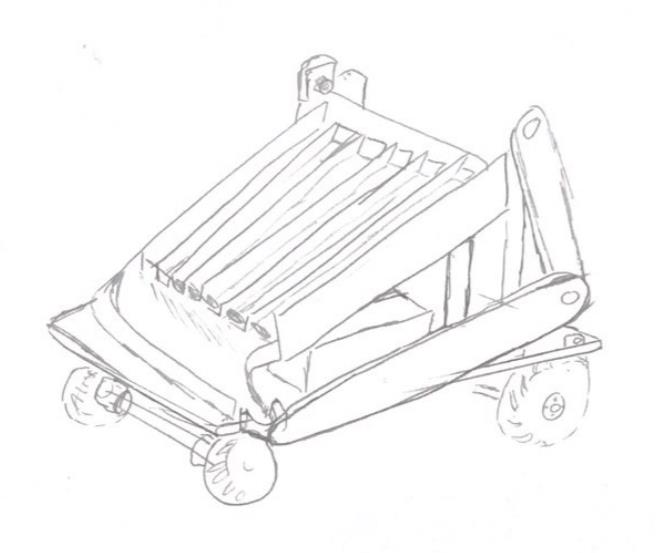
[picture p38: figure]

Team 301 | 14

Figure 4. The color sorting robot

Concept 2.

The following concept, termed “the scorpion,” used biomimicry to develop the general

idea. The scorpion’s tail was mimicked in its design. Fully imitating the scorpion’s tail would

require a large number of motors, so the design was limited to 4 motors in the “tail.” The robot

will still sit on 4 wheels, with the rear wheels driving the robot and the front wheels steering.

Each rear wheel will have an individual motor for increased mobility.

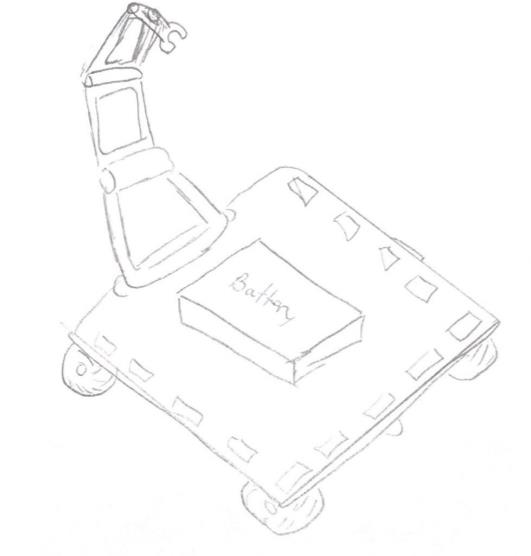
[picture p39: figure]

Team 301 | 15

Figure 5. The scorpion

Concept 3.

Robot to stack Legos that has 2 arms to hold the Lego and stack it and has a

hammerlike appendage on top to make sure the Legos stick together.

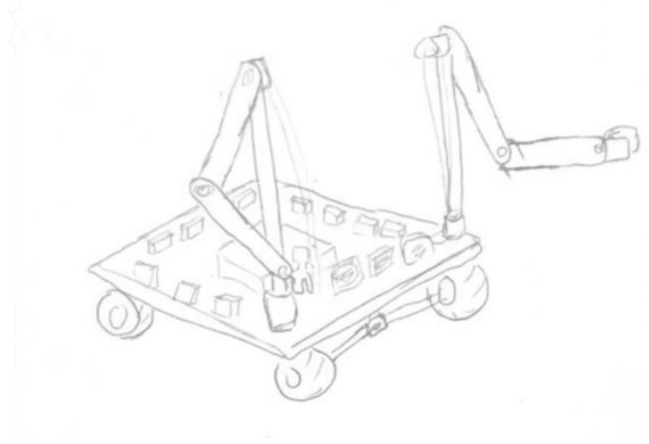
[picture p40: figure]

Team 301 | 16

Figure 6. Robot with two arms.

Concept 4.

The robot uses an elevator and two claws to raise and lower blocks. It will use infrared

sensors to navigate the playfield and avoid the barriers. The navigation will be supplemented

using line following. It will find blocks using sonar and will differentiate between the blocks’

colors and the buttons using a camera. It will have a 4-wheeled base and will be programmed

using C++. The robot has a lift kit, to maximize its height.

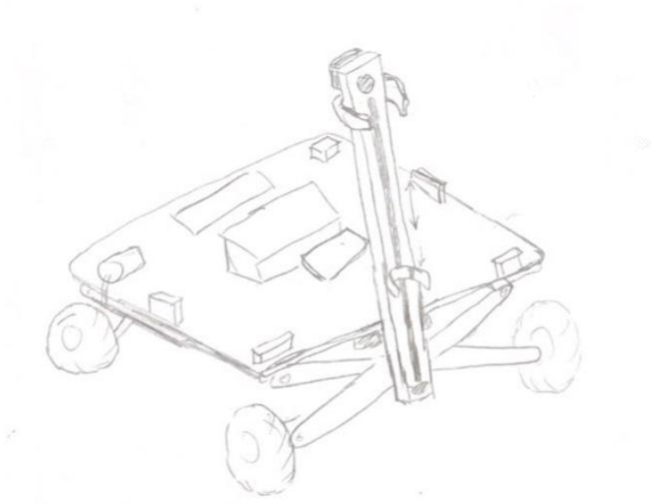
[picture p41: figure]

Team 301 | 17

Figure 7. Robot with two claws and lift kit.

Concept 5.

The robot a slide system on either side to collect the blocks we need and drag them along with

the robot back to the base of the stack. It will use a claw on a track to move around grab the next

block in the sequence and stack it. It will use infrared sensors to navigate the playfield and avoid

the barriers. The navigation will be supplemented using line following. It will find blocks using

sonar and infrared sensors. It will have a 4-wheeled base and will be programmed using C++.

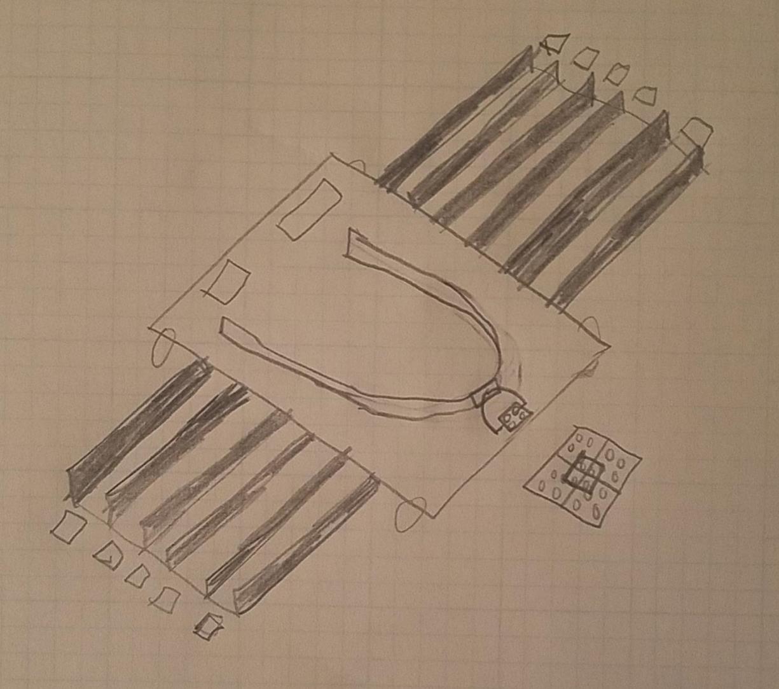
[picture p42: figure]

Team 301 | 18

Figure 8. Robot with slide system

Concept 6.

The robot uses a spring-based elevator in 10 individual hoppers on the robot to store and supply

bricks. It will have a claw track to grab the individual blocks and bring it over to the base for

stacking. It will use infrared sensors to navigate the playfield and avoid the barriers. The

navigation will be supplemented using line following. It will find blocks using sonar and infrared

sensors. It will have a 4-wheeled base and will be programmed using C++.

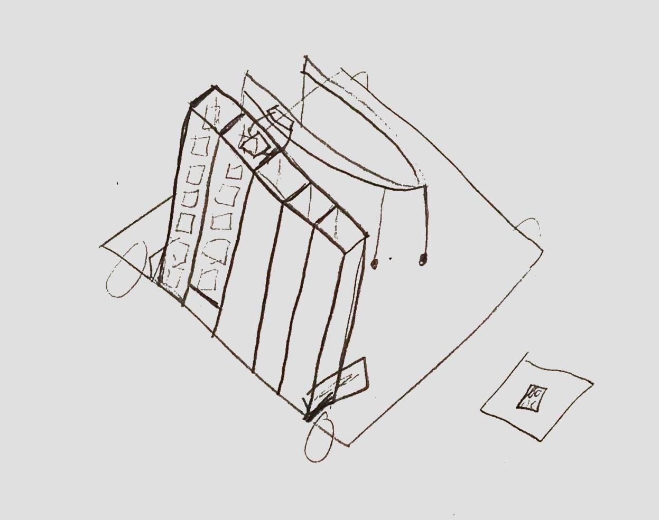
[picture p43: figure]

Team 301 | 19

Figure 9. Spring elevator robot

Concept 7.

The concept of the stingray originated from the need to get the most amount of blocks to

the base in an organized fashion in the most efficient way. The stingray is composed of a net-like

arms which are used to drag the Legos from the bins in an organized fashion all the way to the

base, as depicted on figure 1 and 2.

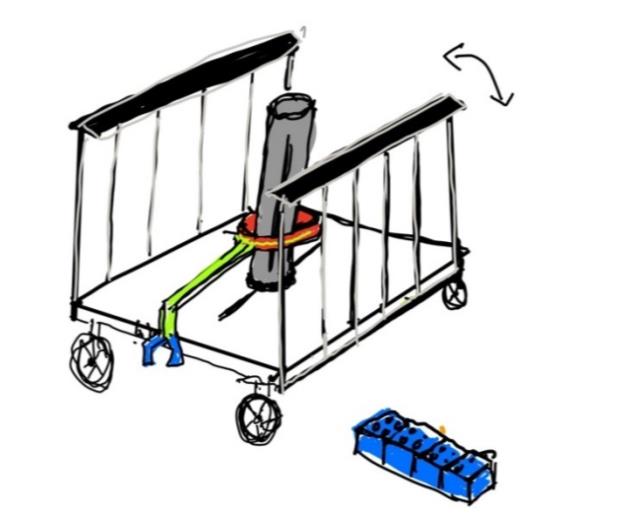
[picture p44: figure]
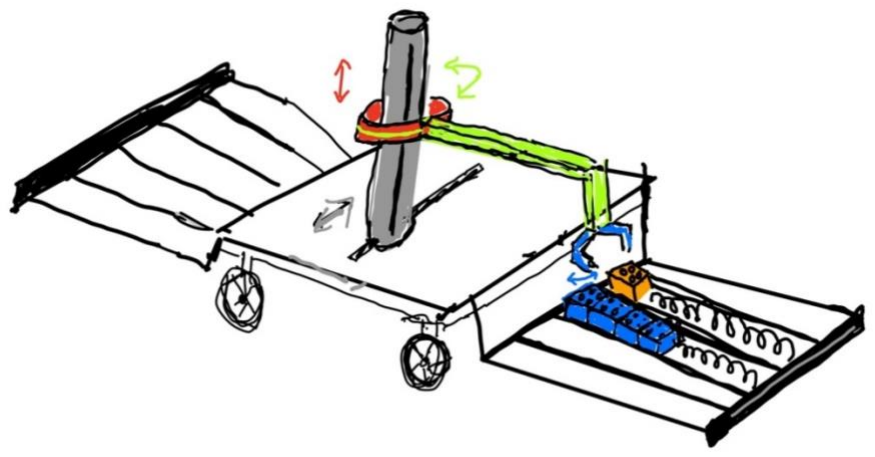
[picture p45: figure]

Team 301 | 20

Figure 10. Stingray design (sketch) - arms folded

Figure 11. Stingray design (sketch) – arms unfolded

### 1.6 Concept Selection

Function and customer needs were used to evaluate the ideas generated in the concept

generation phase. From the 100 generated ideas, the eight most relevant concepts were

Team 301 | 21

considered. The evaluation process was done by using several concept selection tools such as

house of quality table, Pugh matrices, and the analytical hierarchy process. By using all of these

it was possible to make a concept selection.

House of Quality

The house of quality is a design tool of function arrangement. It identifies and classifies

customer needs and identifies their relevance, it also identifies the engineering characteristics

required for those needs and correlates the two. This tool was used to evaluate the six customer

needs present in this project, acceleration, distance from barrier, block height, time to reach

correct bin, end time behavior, and time to locate block within bin. By studying these it was

possible to assign a numerical relevance of each of these needs to the project.

The results obtained after doing the house of quality are shown on table 1. From the

obtained results it can be observed that the block height customer need will play the most

relevant role in the project. This need has a relative weight of 21%, it was followed close behind

by the needs, distance from barrier, time to reach correct bin, and end time behavior all with a

17% relative weight. The needs considered less relevant according to the house of quality are

time to locate block within bin and acceleration with 15% and 13% respectively. A binary

pairwise comparison table was used to evaluate the customer needs, Stack duplo blocks

correctly, mobility, robot volumes, color recognition, speed, automatic shutdown, and button

pushing.

Table 2. Binary Pairwise Comparison

Calculate Weight Factor of Customer Requirements
Customer Requirements | 1 2 3 4 5 6 7 | Total
Stack Duplo Blocks Correctly | - | 1 0 1 1 1 1 | 5

Team 301 | 22
Mobility | 0 | - | 0 1 1 1 1 | 4
Robot Volume | 1 1 | - | 1 1 1 1 | 6
Color Recognition | 0 0 0 | - | 0 1 1 | 2
Speed | 0 0 0 1 | - | 1 1 | 3
Automatic Shutdown | 0 0 0 0 0 | - | 1 | 1
Button Pushing | 0 0 0 0 0 0 | - | 0

It can be observed that the customer most relevant according to the binary pairwise comparison

is the robot volume, with a total of 6 points. Robot volume plays an important role as more

volume will allow more functionality to be added to the robot. The maximum value is fixed by

the competition rules, if the volume of the robot is more than that specified by the competition,

the team will automatically be disqualified. The second most important need is to stack the duplo

blocks correctly, with a total of 5 points. Stacking blocks correctly is the method that will allow

for the largest amount of points to be scored in the least amount of time. The goal of the project

is to score the most amount of points within the given time, so it is logical for this need to play

an important role in the project. This need is followed by mobility, speed, automatic shutdown,

and button pushing, with total points 4,3,2,1, and 0 respectively.

Pugh Matrix

We used a Pugh matrix as another form of concept selection in which we took all of the

engineering characteristics and add weights to the ones we consider more important than others

to be able to make a ranking to see which concept would be the best to pick given their total

score in the criteria. This can be seen in table 3 as well as table 4.

Table 2. Pugh Matrix 1

Team 301 | 23
Engineering Characteristics | Datum | Weights | Scorpion | Robot w/ two arms | Claws and lift kit | Slide System | Spring based elevator | Stingray
Acceleration | 0 | 1 | 1 | 1 | 1 | 1 | 0 | -1
Distance from Barrier | 0 | 1 | 1 | 1 | 1 | 0 | 0 | 1
Block Height | 0 | 2 | 0 | 1 | 0 | 0 | 0 | 1
Time to reach correct bin | 0 | 1 | -1 | -1 | 0 | 1 | -1 | 0
End time behavior | 0 | 1 | 1 | 1 | 1 | 1 | 0 | 1
Time to locate block | 0 | 1 | 0 | -1 | 0 | 1 | 0 | 1
Total Score | - | - | 2 | 3 | 3 | 4 | -1 | 4
Rank | - | - | 5 | 3 | 3 | 1 | 6 | 1

Table 3. Pugh Matrix 2

Engineering Characteristics | Weights | Datum (Scorpion) | Robot with two arms | Slide System | Claws and lift kit | Stingray
Acceleration | 1 | 0 | -1 | -1 | -1 | -1
Distance from barrier | 1 | 0 | 0 | -1 | 0 | 0
Block height | 2 | 0 | 1 | 0 | 1 | 1
Time to reach correct bin | 1 | 0 | 0 | 1 | 1 | 1
End time behavior | 1 | 0 | 0 | 1 | 0 | 1
Time to locate blocks | 1 | 0 | 1 | 1 | 1 | 1
Total | - | - | 1 | 1 | 3 | 4
Rank | - | - | 3 | 3 | 2 | 1

We set the baseline to be zero and if it is better than the baseline we give it a one and if it

is worse than the baseline we give it a negative one however if it is relatively similar to the

baseline we will give it a zero. From our engineering characteristics we gave the most weight to

block height since this determines the maximum size of our Lego stack and having the most

amount of Legos stacked will be important considering our robot is limited in size and since we

will most likely be stacking the Lego in pi order every additional block will give us a

considerable amount more points, for example 10 blocks is 2000 points while 11 blocks is 2420

points giving us a difference of 420 points showing the importance one block makes. From the

Team 301 | 24

first Pugh matrix we got that the stingray and the slide system design were tied for the best

design. To remedy this, we made a second Pugh matrix having the scorpion design as our

baseline and comparing the other designs to it to have another point of reference. Applying the

same rules as the first Pugh matrix we came with the results that the stingray was better than the

slide system finally declaring the stingray design as the best option according to the Pugh

matrices we made.

Analytical Hierarchy Process

For the last analysis method, we used an AHP (analytical hierarchy process) to determine

which idea to select. These can be seen from Table 4, the weights we calculated can be seen in

Table 5 and the final values for each design in Table 6. For the AHP we put the concepts in the

first column as well as a datum to have as a reference point and we put the criteria on the first

row. After this we arbitrarily rated how good we thought a given design would be at given

criteria. Using the rules given to us to make an AHP we took the reciprocal and made weights for

each category. After that we added the sum of the results with the weights to get the final results.

This method has its advantages in that it is a more mathematically rigorous method using

principles of linear algebra and has more weights than the ones used in the Pugh matrix.

Team 301 | 25

Table 4.
Final AHP Matrix

Final Matrix Transposed

| Acceleration | Distance from Barrier | Block height (raising and lowering) | Time to Reach Correct Bin (Color Determination) | End Time behavior | Time to locate block within bin
Datum - Color Sorting | 0.047 | 0.091 | 0.102 | 0.249 | 0.106 | 0.069
Scorpion | 0.304 | 0.284 | 0.117 | 0.059 | 0.199 | 0.072
Robot with two arms | 0.161 | 0.146 | 0.091 | 0.044 | 0.206 | 0.238
Claws and lift kit | 0.259 | 0.213 | 0.318 | 0.209 | 0.118 | 0.074
Slide system | 0.061 | 0.041 | 0.058 | 0.116 | 0.181 | 0.117
Spring-based elevator | 0.116 | 0.103 | 0.151 | 0.104 | 0.038 | 0.076
Stingray | 0.052 | 0.123 | 0.163 | 0.219 | 0.153 | 0.355
Table 5.
Criteria Weights

Criteria Weights
0.157
0.054
0.176
0.211
0.065
0.337
Table 6.
Concept and Alternative Value
Concept | Alternative Value
Datum - Color Sorting | 0.113
Scorpion | 0.133
Robot with two arms | 0.152
Claws and lift kit | 0.185
Slide system | 0.098
Spring-based elevator | 0.100
Stingray | 0.219

Team 301 | 26

However, we did choose arbitrary numbers since we are only speculating how the designs

will perform in a given task compared to the other designs. After completing all these steps for

each design we ended up with the values on table 7 which indicate that given the values we

chose the best design is the stingray. Following the completion of all the steps for each design

we ended up with the values on table 7 which indicate that given the values we chose the best

design is the stingray.

Final Concept

After evaluating the results obtained from the analytical hierarchy process, the stingray

design is the concept that will be selected for the project. The results obtained for the stingray on

the AHP final matrix, alongside the criteria comparison weight, and the concept and alternative

value tables (Table 4, Table 5, andTable 6 respectively), are the highest obtained results within

each of the tables. The concept of the stingray originated from the need to get the most amount

of blocks to the base in an organized fashion in the most efficient way. The stingray is composed

of a net-like arms which are used to drag the Legos from the bins in an organized fashion all the

way to the base, as depicted in Figure 12 and Figure 13.

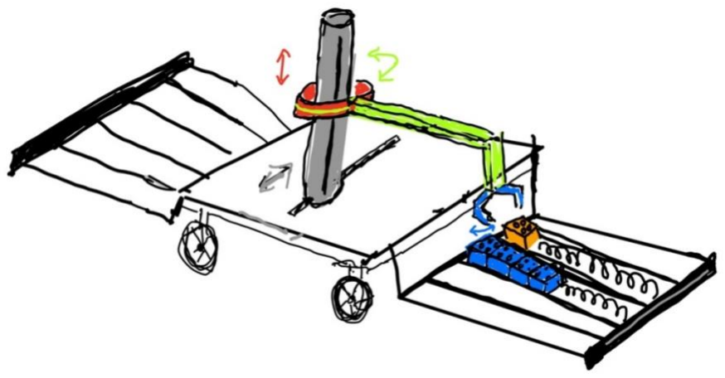
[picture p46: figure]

Team 301 | 27

Figure 12. Stingray design (sketch) - arms folded

Figure 13. Stingray design (sketch) - arms unfolded

These arms will eliminate the need for a camera-based recognition system that will

determine the color of the blocks, as the design will know the color of blocks due to their

position within the arm. The design of the arms will also eliminate the need for the robot to

travel back and forth from the base to the bins to get more Lego blocks of a single color. The

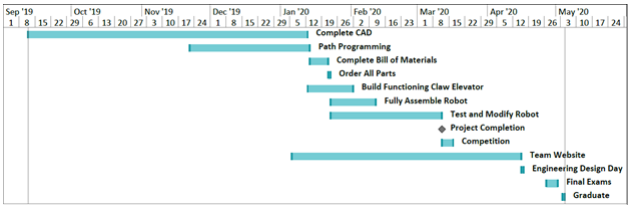
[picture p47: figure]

Team 301 | 28

robot will only need to go once to each bin, and from there it will collect all the necessary blocks

for the stack within that bin. From there an arm, composed of a lift and a claw that moves 360

degrees pick the Lego Blocks and stacks them correctly on the base.

### 1.8 Spring Project Plan

The following Gantt chart shows our team’s plan for the spring semester. By the end of

this fall semester, we aim to have a functioning line following robot so we can have the frame

and basic path programming by the end of the semester. Considering we have the replica of the

arena that will be used in the competition, we will have an accurate representation of how our

line following will roughly be by the end of the fall semester.

Figure 14. Gantt chart.

By the start of the spring semester we want to have a complete CAD of the entire robot so

we can have an idea of how everything will fit and how we can assemble it. Also, near the

beginning of the spring semester we want to have the path programming down so we can focus

Team 301 | 29

on the rest of the robot. Even though it might seem like having the line following is most of the

path programming that is not the case since we need to move the robot out of the line to pick up

the Legos and from there back to the line and follow the sequence of Legos we want so we will

have to work on all that to make a successful robot that can follow the path it needs to. By the

beginning of February, we want to have a functioning claw elevator since that is the most

important part of the robot along with the path following. By February 19 we want to put all

this together and have a fully assembled robot since we want to have some time to be able to

work on it and make any fixes that will be necessary since it is almost guaranteed that something

will go wrong or we will make some changes to optimize the robot. By the end of February, we

want to have the project complete meaning that we want the robot to be fully functioning and

complete the goals we set for it. This will give us two weeks to make any adjustments we need

for the competition. March 14th is the competition so by that point we will have to hope that our

efforts of the previous months will give us a good result. After the competition the bulk of our

work is done, and we only need to concern ourselves with finishing the assignments for senior

design. After that we concern ourselves with graduating in May 2nd.

Table 7.
Spring Milestones
Activity | Expected Completion Date
Completed CAD | January 12, 2020
Path Programming | January 13, 2020
Completed Bill of Materials | January 21, 2020

Team 301 | 30
All parts ordered | January 22, 2020
Functioning Claw Elevator | February 1, 2020
Fully Assembled Robot | February 11, 2020
Testing | March 11, 2020
Project Completed | March 11, 2020
Competition | March 16, 2020
Team Website Completion | April 15, 2020
Engineering Design Day | April 16, 2020
Final Exams | May 1, 2020
Graduation | May 2, 2020

Team 301 | 31

Chapter Two: EML 4552C

### 2.1 Spring Plan

Project Plan.

Build Plan.

Team 301 | 32

Team 301 | 33

Appendices

Team 301 | 34

Appendix A: Code of Conduct

## FAMU/FSU College of Engineering

## Department of Electrical and Computer Engineering

## Code of Conduct

## Team 301 (IEEE SoutheastCon Student Hardware Competition) Names: Isabel Barnola David Bowen Diego Campos Alex Ndekeng Abiel Souverain

## Date 9/20/2019

Team 301 | 35

## Mission Statement

Team 301 is committed to ensuring a positive work environment that supports professionalism, integrity, respect, and trust. Every member of this team will be contributing full effort to the creation and maintenance of such an environment in order to bring out the best in all of us as well as this project.

## Roles

Each team member is delegated a specific role based on their experience and skill sets and is responsible for all here-within:

## Team members:

Team Leader: David Bowen
Manages the team as a whole; develops a plan and timeline for the project, delegates tasks among group members, and finalizes all documents and provides input on other positions where needed. The team leader is responsible for promoting synergy and increased teamwork. If a problem arises, the team leader will act in the best interest of the project. He is the point of contact between team members, advisors, and sponsors. The team leader takes the lead in organizing, planning, and setting up meetings. In addition, he is responsible for keeping a record of all correspondence between the group and ‘minutes’ for the meetings. Finally, he gives or facilitates presentations by individual team members and is responsible for overall project plans and progress.

Lead Power Electronics Engineer: Alex Ndekeng
The lead Power Electronics Engineer is responsible for putting together the various power electronic and controls of the robot; assembling the wiring for the parts provided by the other team members. This role will also involve testing the parts for the desired electrical outputs.

Lead Software Engineer: Isabel Barnola
The lead software engineer is responsible to design the underlaying architecture of the software that will control the robot, and to oversee all coding done by any other team member. Ensures that completed product controls the robot.

Lead Design Engineer: Abiel Souverain
The lead design Engineer is responsible for the 3D CAD models of the product and the drawings of the cad models. Ensures completed product can withstand necessary forces. They will possibly provide an analysis in ProE.

Team 301 | 36

Lead Signal Process Engineer: Diego Campos
The lead signal engineer will be responsible for making sure that every interconnected device in the robot such as sensors and cameras will successfully communicate with one another in an efficient manner.

Lead Robotics Engineer: David Bowen
The lead robotics engineer is responsible for the assembly of the robot and ensuring that all the parts (electrical and mechanical) mesh and work together. They will also be accountable for leading the testing of the robot with the lead software engineer.

## All Team Members:

- Work on certain tasks of the project
- Buys into the project goals and success
- Delivers on commitments
- Adopt team spirit
- Listen and contribute constructively (feedback)
- Be effective in trying to get message across
- Be open minded to other’s ideas
- Respect other’s roles and ideas
- Be ambassador to the outside world in own tasks

## Communication

The main form of communication will be basecamp among the group, as well as through regular meetings of the whole team. Email will be a secondary form of communication for issues not being time sensitive. Email will also be used for communication with our advisors and professors. For the passing of information, i.e. files and presentations, basecamp will be the main form of file transfer and proliferation.
Each group member must have a working basecamp and email for the purposes of communication and file transference. Members must check their basecamp and emails at least twice a day to check for important information and updates from the group. Members will be initially informed via the Outlook calendar, so it is very important that each group member checks their email frequently. Completed files will be uploaded to basecamp but working documents will be uploaded to Office 365.
If a meeting must be canceled, an email must be sent to the group at least 6 hours in advance. Any team member that cannot attend a meeting must give advance notice of 6 hours informing the group of his absence. Reason for absence will be appreciated but does not need to be specific. Meetings will be given a priority level from 1 – 3, with 3 being the highest priority (cannot miss). Repeated absences in violation with this agreement will not be tolerated.

Team 301 | 37

## Team Dynamics

The students will work as a team while allowing one another to feel free to make any suggestions or constructive criticisms without fear of being ridiculed and/or embarrassed. If any member on this team finds a task to be too difficult it is expected that the member should ask for help from the other teammates. If any member of the team feels they are not being respected or taken seriously, that member must bring it to the attention of the team for the issue to be resolved. We shall NOT let emotions dictate our actions. Everything done is for the benefit of the project and together everyone achieves more.

## Ethics

Team members are required to be familiar with the NSPE Engineering Code of ethics as they are responsible for their obligations to the public, the client, the employer, and the profession. There will be stringent following of the NSPE Engineering Code of Ethics.

## Dress Code

Team meetings and Adviser meetings will be held in casual attire or Power Ranger costumes. Sponsor meetings and group presentations will be business formal to formal as decided by the team per the event.

## Weekly and biweekly Tasks

Team members will participate in all meetings with the sponsor, adviser and instructor. During said times ideas, project progress, budget, conflicts, timelines and due dates will be discussed. In addition, tasks will be delegated to team members during these meetings. Repeat absences will not be tolerated.

## Decision Making

It is conducted by consensus and majority of the team members. Should ethical/moral reasons be cited for dissenting reason, then the ethics/morals shall be evaluated as a group and the majority will decide on the plan of action. Individuals with conflicts of interest should not participate in decision-making processes but do not need to announce said conflict. It is up to each individual to act ethically and for the interests of the group and the goals of the project. Achieving the goal of the project will be the top priority for each group member. Crucial decisions will be made by the entire team. Smaller decisions will be made by individuals or a subset of the team. Below are the steps to be followed for each decision-making process:

- Problem Definition – Define the problem and understand it. Discuss among the group.

Team 301 | 38
- Tentative Solutions – Brainstorms possible solutions. Discuss among group most plausible.
- Data/History Gathering and Analyses – Gather necessary data required for implementing Tentative Solution. Re-evaluate Tentative Solution for plausibility and effectiveness.
- Design – Design the Tentative Solution product and construct it. Re-evaluate for plausibility and effectiveness.
- Test and Simulation/Observation – Test design for Tentative Solution and gather data. Re-evaluate for plausibility and effectiveness.
- Final Evaluation – Evaluate the testing phase and determine its level of success. Decide if design can be improved and if time/budget allows for it.

## Conflict Resolution

In the event of discord amongst team members the following steps shall be respectfully employed:
- Communication of points of interest from both parties which may include demonstration of active listening by both parties through paraphrasing or other tool acknowledging clear understanding.
- Administration of a vote, if needed, favoring majority rule.
- Chess Game
- Team Leader intervention.
- Instructor will facilitate the resolution of conflicts.

Team 301 | 39

Appendix B: Functional Decomposition

Figure 15. Functional Decomposition Hierarchy Robot

Push | Push Buttons
Stack | Stack Duplo Blocks

### Lift blocks

### Lower blocks

### Navigate

### Navigate the play field

### Avoid barriers

### Find Blocks

### Recognition

Recognize Duplo block | Differentiate between colors of blocks
Recognize Buttons | Differentiate between lit and unlit button

Team 301 | 40

Table 8.
Cross-Reference Table
| System
Function | Push | Stack | Navigate | Recognition

Navigate the play field

Avoid Barriers

Push Buttons

Find Blocks

Lift Duplo Blocks

Lower Duplo Blocks

Differentiate between blocks

Differentiate between buttons

Team 301 | 41

Appendix C: Target Catalog

Table 9.
Functions, Metrics, and Targets
Functions | Metrics | Target
Navigate the Play Field* | Number of path combinations
| completed | 10
Avoid Barriers | Distance from barrier (inches) | >1 in
Push Buttons | Depth of button push (inches) | 1/8 in
Find Block | Time to locate block
| (seconds) | <5 sec
Lift Duplo Block | Height reached (inches) | ~1.5 block height above
| | previous block
Lower Duplo Block | Height reached (inches) | 1 block height above previous
| | block
Differentiate between buttons | Time to locate proper button
| (seconds) | <10 sec
Differentiate between blocks | Time to reach correct bin
| (seconds) | <20 sec

* Indicates Critical Targets

Appendix D: Concepts

1. Basic, 4-wheeled robot, swiveling arm in center with 2 joints and sonar sensors for

navigation.

2. 3 wheels, 2 in front, omnidirectional in rear, same arm as idea 1
3. Arm anchored at 12” height, 3 joints (can reach higher than 12”)
4. Design 1, infrared sensors for navigation
5. Use color recognition and sonar to find blocks in the correct order
6. Arm that lifts block and stacks upside down (like garbage truck) stack entire stack at the

end on platform.

Team 301 | 42
7. Robot stacks in pi order in increments of 10 and places stack near platform and puts the

stacks together at the end.

8. Crane arm that can be extended when initialized (slider)
9. Robot stores a certain amount of each color needed at a time on body and places in

correct order on platform.

10. The robot has a sorter on its body with blocks that slide in. A gate opens releasing the

next color necessary in the stacking sequence.

11. Elevator arm used to stack blocks from below
12. Robot with leg like extremities used to increase height and to move through field.
13. Car like robot with lift kit, to maximize height of robot.
14. Two robots, one gathers Lego Blocks at base, another robot stacks them in correct order.
15. Robot with up to 10 arms, picks ten stacked towers, move ten towers to base and from

there it takes each Blocks in correct Pi order and stacks them at base.

16. Same idea as before, though Robot only stacks in correct order until sometime within the

three minutes, then it stacks the remaining towers on top of the stack that’s on the base.

17. Robot has a tray where it stores ten stacked towers to then later use to stack at base.
18. Scissor lift arm that stacks blocks.
19. Robot gathers all blocks and arranges the blocks in Pi order horizontally and then flips

the stacked tower vertically before setting it down in base.

20. Car like robot with lift kit and a scissor lift to maximize its height.
21. 2 robots one stacks Legos like the one in idea 1 the other pushes buttons in pi order

Team 301 | 43
22. Same as before except second robot pushes one button 100 times so it doesn’t have to

move much

23. The robot has a pincer like appendage at the back that picks up the Lego (like a scorpion)
24. Uses line following sensors to guide itself to the blocks general direction then uses sonar

sensors same as 1

25. Same as 24 except it uses hard coded locations after the line sensor instead of sonar
26. Robot to stack Legos that has 2 arms to hold the Lego and stack it and has a hammerlike

appendage on top to make sure the Legos stick together

27. Robot to push button that has 4 arms and extends them to push the correct ones in pi

order

28. A robot that stacks Legos but detects if they fell over and if they do it starts from the last

one standing

29. A robot that stacks the Legos from the bottom up and holds it at the end to keep it stable

but at the opposite end from where judges will see

30. The robot stacks Lego blocks on a mobile platform
31. The legos are setup upside down, so that robot can flip them as they are picked up
32. The pickup motion is the same as using two hands to pick up an open box and putting the

box on your head.

33. From the mobile platform, the robot will locate and hold the stack. (without pushing it

over) the arms that pick up blocks can be used to hold the stack.

34. The robot will raise the blocks from the mobile platform and set it on top of the stack.
35. If order isn’t a priority, and the arm is strong enough, the robot will raise from the bottom

and push a new stack on the bottom.

Team 301 | 44
36. Robot that has a tail like a scorpion and picks up blocks by “stinging” them.
37. Robot can use omni direction wheels and sensors to facilitate sideways movement and

finely adjust the position of the robot with respect to the stack of legos so that the arms

can be more precise in stacking blocks.

38. The robot can use sensors in front of the vehicle to determine when it has reached the

white lines and markings (center of the playfield) and be able to determine whether it

should turn left or right towards other bins or head to the Lego stacking platform.

39. The robot will track the white lines on the field to navigate. The robot will pick up the

legos with a claw hand. It will stack 5 bricks at a time within the robot and stack each

stack on the base.

40. The robot will use a “spatula” to pick up the blocks.
41. There will be 2 robots, one will collect the blocks and deliver it to the 2nd bot. The other

will be stationed at the base and be stacking the blocks brought to it by the 1st robot.

42. There will be 2 robots, the 1st will push buttons on the wall. The 2nd will collect and stack

blocks.

43. 3 robots, 1st will push the buttons, 2nd will collect and deliver the blocks over to the base,

and 3rd will stack the blocks on the base.

44. The robot has an elevator with 2 claws that grabs a block and lifts up, then the lower claw

will lift the next block up to the stack and force them together, and it will repeat the

process until it has 10 together. Then it will place the stack on the base and repeat until

the time is up.

Team 301 | 45
45. Robot with 5 bins on each side of the robot to hold the blocks of each color. Arms will

take from the bins as needed and stack the blocks.

46. Robot will collect blocks from each bin 1 at a time; drive it over to the base and stack

them 1 at a time.

47. Robot will push the buttons using a solenoid.
48. Robot will push the buttons using a piston.
49. 10 robots that will each go collect 1 block at a time and bring them over to the base and

stack them.

50. 3 robots, 1st will grab bricks from the left side of the fields, 2nd will grab bricks from the

right side, and 3rd

Table 10.
Morphological Chart
Push Buttons | Lift/Lowe r blocks | Navigate the playfield | Avoid Barriers | Find Blocks | Differentiat e between blocks | Differentiat e between buttons | Motion | Coding Language
Piston | Arm and claw | Infrared | Infrared | Sonar | Camera | Camera | 4 Wheels | C++
Navigatio n | Elevator and two claws | Sonar | Sonar | Infrared | Hard coding Locations | Hard coding locations | 3 Wheels | C
| Elevator and one claw | Infrared and sonar | Infrared and sonar | Camera | | | Tracks | Python
| | Hardcodin g locations | Hard coding locations | Proximit y sensor | | | Spheric al Wheels | MATLA B
| | Camera | Camera | | | | Legs | Java
| | Line following | Proximit y sensor
51. The robot uses an arm and claw to lift and lower the blocks. Infrared sensors will be used

to navigate the playfield and avoid barriers. It will use sonar to find the blocks and a

Team 301 | 46

camera to differentiate between blocks and buttons. The robot will sit on a 4-wheeled

base and its motion will be coded using C++. The robot will push the buttons using a

piston.

Team 301 | 47

References

Electronics, T. (2017, March 25). Universal Robots vision-based LEGO DUPLO stacker.

Retrieved from https://www.youtube.com/watch?v=fLyhVfCzkio

Radford, R. (2019, June 1). southeastcon2020. Retrieved from github:

https://github.com/ncgadgetry/southeastcon2020/blob/master/Rules/PiDayRules_Jun1_20

19.pdf

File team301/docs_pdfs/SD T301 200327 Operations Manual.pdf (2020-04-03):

Running head: OPERATIONS MANUAL | 1

Operations Manual

Isabel Barnola, David Bowen, Diego Campos, Alex Ndekeng, Abiel Souverain

FAMU-FSU College of Engineering

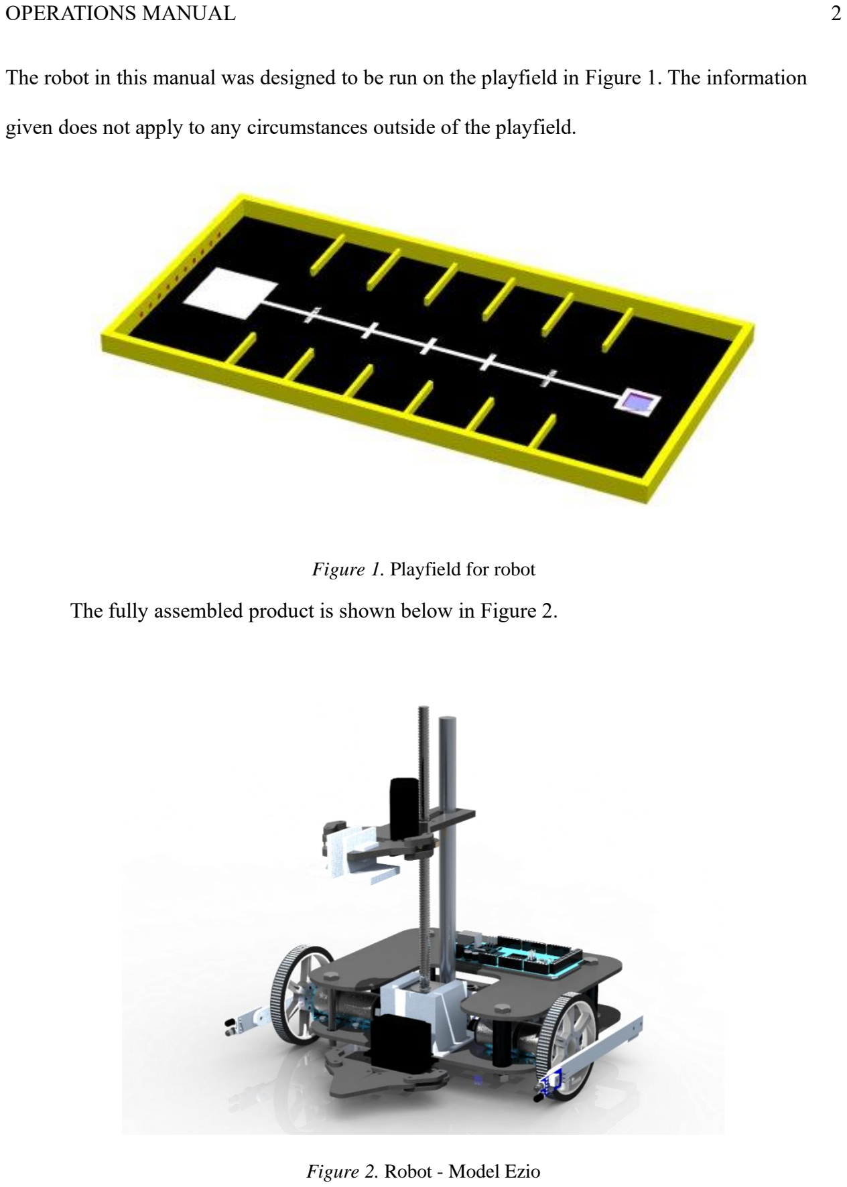
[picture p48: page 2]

OPERATIONS MANUAL | 2

The robot in this manual was designed to be run on the playfield in Figure 1. The information

given does not apply to any circumstances outside of the playfield.

Figure 1. Playfield for robot

The fully assembled product is shown below in Figure 2.

Figure 2. Robot - Model Ezio

Components

- 1x Arduino Mega 2560
- 1x A4988 Stepper Motor Drive Carrier
- 1x 2×15A DC Motor Driver
- 1x Continuous Rotation Servo - FS5103R
- 1x Hitec servo
- 2x Pololu 99:1 Metal Gearmotor 25Dx69L mm LP 6V with 48 CPR Encoder
- 2x Pololu Metal DC motor mounts
- 2x Pololu Pololu Multi-Hub Wheel 80x10mm
- 1x Recessed Flange-Mount Ball Transfer
- 1x Pololu Stepper Motor with 28cm Lead Screw: Bipolar, 200 Steps/Rev, 42×38mm, 2.8V,

1.7 A/Phase, cut to 25cm

- 1x 10in Aluminum Guide Rod
- 9x Obstacle Avoidance IR Sensor
- 1x Assorted Jumper Wires
- 1x 9V Battery
- 1x 12V 2200mAh Li-po Battery

Machined Parts – Drawings on page 10

1x Lower base

1x Upper base

1x 3-IR L-bracket

2x IR L-bracket

2x Side-IR L-bracket

2x Side-IR Arm

1x Stepper Mount

1x Upper Claw

1x Lower Claw

Hardware

- 4x ¼-20 – 1 1/4" Hex bolts
- 8x ¼-20 nuts
- 100x m3x14mm screws
- 100x m3x14mm flat screw
- 100x m3x18mm screws
- 100x m3x12mm screws
- 100x m3 locknuts

Wiring Diagram

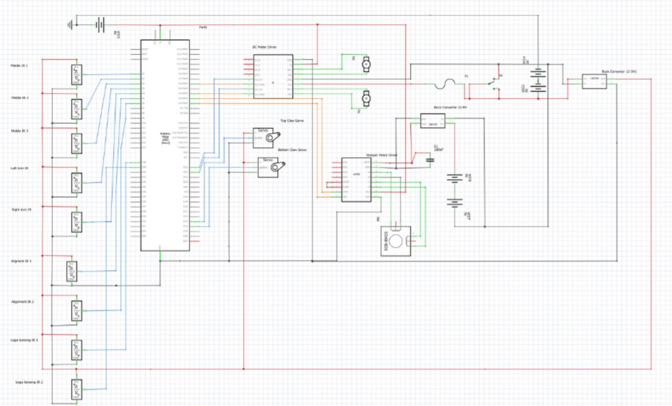
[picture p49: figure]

Pseudocode

The following code gives an example of how the software for the robot should be written

to achieve proper function. The first section contains the main code and its organization. The

following section contains the subfunctions used, which include stacking and line following. The

stacking function incorporates the use of the stepper motor lead screw as well as the upper and

lower claws, controlled by the servos. Because the servo used by the upper claw is a continuous

rotation servo, the power to it must be cycled so that the motor does not close too far.

Main code

/*
FILE : Stacking_challenge_7digits
DESCRIPTION: 1st Challenge of SoutheastCon Hardware competition 2020 AUTHOR : ISABEL BARNOLA

DATE: 03/03
*/

// ================================================================ // MOTORS
// ================================================================ #define L_Forward HIGH //LOW
#define R_Forward LOW //HIGH

#define L_Backward LOW //HIGH

#define R_Backward HIGH //LOW #define plus_factor 5

#define alignement_factor 10 #define go_to_factor 6

#define turn_speed 50

#define turn_speed1 600

int speed_R = 66;// MAX = 255 int speed_L = 62; // MAX = 255 int slow_R = 55;
int slow_L = 55;

//-----------------------
// Motor : Right
//-----------------------
// M1 PWM
//ORANGE
int R_ME = 3; //Enable Pin of the Right Motor (must be PWM) // M1 EN
// YELLOW
int R_M1 = 23; //Control Pin

//-----------------------
// Motor : Left
//-----------------------
// GREEN
int L_ME = 2; //Enable Pin of the Left Motor (must be PWM) // BLUE
int L_M1 = 22;

int dir = 0;
int cnt = 0;

long previousMillis = 0;
long currentMillis = 0;
int interval = 1000;

// ================================================================ // ENCODERS
// ================================================================ #include "mrobot.h" //Provided by Dr. Chuy

// ================================================================ // STACK
// ================================================================ #include<Servo.h>
#include <Stepper.h>

// change this to fit the number of steps per revolution for your motor const int stepsPerRevolution = 200;
Servo servo_top, servo_bot;
Stepper myStepper(stepsPerRevolution, 4, 5, 6, 7);
int ir = 5;

//Servo position for each claw
int bopen = 180;
int bclose = 0;
int topen = 80;
int tclose = 110;

// direction of stepper
const int up = 1;
const int down = -1;

// Position of claw
float pos_claw = 0;

// Stack height
float stack = 0;

// ================================================================ // IR Sensor
// ================================================================ //-----------------------
// Sensor: Right
//-----------------------
const int right_sensor_pin =10; // ORANGE int right_sensor_state;

//-----------------------
// Sensor: Left
//-----------------------
const int left_sensor_pin = 11; // BLUE int left_sensor_state;

//-----------------------
// Sensor: Middle
//-----------------------
const int middle_sensor_pin = 12; // WHITE int middle_sensor_state;

//-----------------------
// Sensor: Left arm
//-----------------------
const int left_arm_sensor_pin = 13; // GREEN int left_arm_sensor_state;

//-----------------------
// Sensor: Right arm
//-----------------------
const int right_arm_sensor_pin = 28; // BLUE int right_arm_sensor_state;

//-----------------------

// Sensor: FRONT Right
//-----------------------
const int front_right_pin = 29; // GREEN int front_right_sensor_state;

//-----------------------
// Sensor: FRONT left
//-----------------------
const int front_left_pin = 30; // YELLOW int front_left_sensor_state;

//-----------------------
// Sensor: low right
//-----------------------
const int low_right_pin = 31; // blue int low_right_sensor_state;

const int led_r = 33;

//-----------------------
// Sensor: low left
//-----------------------
const int low_left_pin = 32; // green int low_left_sensor_state;

const int led_l = 34;

// ================================================================ //TURN_BIN
// ================================================================ //Left
#define t_back_tlb | 16 // time to back up on left

#define time_turn_lb | 1300 // time to turn on left

//Right
#define t_back_trb 16//1000 // time to back up on right

#define time_turn_rb 18//1200 // time to turn on right

// ================================================================ //TURN_LINE
// ================================================================ //Left
#define t_back_tll | 300 // time to back up on left

//#define time_turn_l_l | 1000 // time to turn on left
int time_turn_l_l[] = {18,0};
int ll = 0;
// Right
#define t_back_tlr | 600 // time to back up on right

//#define time_turn_r_l | 1100 // time to turn on right
int time_turn_r_l[] ={13,13};
int rl = 0;

// ================================================================ //TURN_BIN 180
// ================================================================ #define time_turn_180_r 2200000
#define time_turn_180_l 2100000

// ================================================================ //TURN_BIN 180
// ================================================================ //Left
#define t_back_tlb_180 | 700 // time to back up on left

#define time_turn_lb_180 | 1200 // time to turn on left

//Right
#define t_back_trb_180 | 850//1000 // time to back up on right

#define time_turn_rb_180 | 1000//1200 // time to turn on right

// ================================================================ //TURN_LINE 180
// ================================================================

//Left
#define t_back_tll_180 | 300 // time to back up on left

#define time_turn_l_l_180 | 1000 // time to turn on left

// Right
#define t_back_tlr_180 | 600 // time to back up on right

#define time_turn_r_l_180 | 1200 // time to turn on right

int e_turn = 0;
int pos = 0; // used to determine robot's current position

// ================================================================ // STATES
// ================================================================ #define STOP 0
#define LINE_FOLLOWING 1

#define TURN_RIGHT_BIN 2

#define TURN_LEFT_BIN 3

#define TURN_RIGHT_LINE 4

#define TURN_LEFT_LINE 5

#define BACK_TO_LINE 6

#define STACK | 7

#define OPPOSITE_R | 8

#define GO_TO_BIN | 9

#define OPPOSITE_L | 10

#define test | 11

#define aligned | 12

const int num_states_to_do = 38;
int states_to_do[num_states_to_do] = { LINE_FOLLOWING,
TURN_LEFT_BIN,
GO_TO_BIN,
STACK,
BACK_TO_LINE,
TURN_RIGHT_LINE,
aligned,

LINE_FOLLOWING,
TURN_LEFT_BIN,
GO_TO_BIN,
STACK,
BACK_TO_LINE,
test,
aligned,
GO_TO_BIN,
STACK,
BACK_TO_LINE,
STOP,
test,
aligned,
GO_TO_BIN,
STACK,
BACK_TO_LINE,
TURN_RIGHT_LINE,
aligned,
LINE_FOLLOWING,
TURN_RIGHT_BIN,
GO_TO_BIN,
STACK,
BACK_TO_LINE,
TURN_LEFT_LINE,
aligned,
LINE_FOLLOWING,
aligned,
STACK,
BACK_TO_LINE,
STOP
};

int state = LINE_FOLLOWING;
int itr_s = -1; // used to iterate through array of states #define RIGHT 10
#define LEFT 11

int last_dir = 0;

// ================================================================ //LINE_FOLLOWING
// ================================================================ #define BLACK HIGH
#define WHITE LOW

#define plus_dir 1

#define minus_dir -1

const int bins_to_go_LF = 3; // the total number of bins to go with LF int white_lines = 0;
int lines_to_do[] = {3,2,2,2};
//int direc_to_do[bins_to_go_LF] = {plus_dir};
int do_lf = 0;

// ================================================================ //FUNCTIONS
// ================================================================ #include "FUNCTIONS.h"

// ================================================================ // SETUP
// ================================================================ void setup()
{ // opening setup

//-----------------------
// Motors
//-----------------------
pinMode(R_M1, OUTPUT); // Right pinMode(L_M1, OUTPUT); // Left

//-----------------------
// IR Sensors
//-----------------------
pinMode(right_sensor_pin, INPUT); // Right pinMode(left_sensor_pin, INPUT); // Left pinMode(middle_sensor_pin, INPUT); // Middle pinMode(left_arm_sensor_pin, INPUT); // left arm pinMode(right_arm_sensor_pin, INPUT); // right arm
pinMode(low_left_pin, INPUT); | // lower left
pinMode(low_right_pin, INPUT); | // lower right
pinMode(front_left_pin,INPUT); | // front left
pinMode(front_right_pin,INPUT); | // front right
pinMode(led_r,OUTPUT);
pinMode(led_l,OUTPUT);

//----------------------
// Encoders
//----------------------
encoder_init();

//----------------------
// Stacking
//----------------------
servo_top.attach(9);
servo_bot.attach(8);
myStepper.setSpeed(275);

Serial.begin(9600); // For serial print (debugging)

}
// closing setup

int ii = 0;
// ================================================================ // LOOP
// ================================================================ void loop()
{ // opening loop

//-------------------------------------// STATE: Update
//-------------------------------------

state = set_state();
//-------------------------------------// IR Sensors: READ
//-------------------------------------read_ir();

//-------------------------------------// FSM
//-------------------------------------

switch(state)
{//opening switch

//-----------------------
//LINE_FOLLOWING
//-----------------------
case LINE_FOLLOWING:
{ //opening LINE_FOLLOWING

print_state(); // prints the current state to serial port Serial.println("LINE_FOLLOWING");
// Line following - parameters set on top line_following(lines_to_do[do_lf],plus_dir);
do_lf = do_lf + 1;
}
//closing LINE_FOLLOWING
break;

//-----------------------
// TURN_RIGHT_BIN
//-----------------------
case TURN_RIGHT_BIN:
{ //opening TURN_RIGHT_BIN
print_state(); // prints the current state to serial port Serial.println("TURN_RIGHT_BIN");
delay(100);
back_before_turn(t_back_trb);

delay(200);
turn_left_bin(time_turn_rb); last_dir = RIGHT;
}
//closing TURN_RIGHT_BIN
break;

//-----------------------
//TURN_LEFT_BIN
//-----------------------
case TURN_LEFT_BIN:
{ //opening TURN_LEFT_BIN
print_state(); // prints the current state to serial port //print_state(); // prints the current state to serial port Serial.println("TURN_LEFT_BIN");
delay(100);
back_before_turn(t_back_tlb); turn_right_bin(time_turn_lb); last_dir = LEFT;
}
//closing TURN_LEFT_BIN
break;

//-----------------------
//TURN_RIGHT_LINE
//-----------------------
case TURN_RIGHT_LINE:
{ //opening TURN_RIGHT_LINE
print_state(); // prints the current state to serial port Serial.println("TURN_RIGHT_LINE"); delay(100);
back_off_time(t_back_tlr);
back_off(speed_R, speed_L); back_off(speed_R, speed_L); //back-off();
delay(200);
long int t = time_turn_r_l[rl];

rl++;
turn_right_line(t);
back_before_turn(3);
}
//closing TURN_RIGHT_LINE
break;

//-----------------------
//TURN_LEFT_LINE
//-----------------------
case TURN_LEFT_LINE:
{ //opening TURN_LEFT_LINE
print_state(); // prints the current state to serial port Serial.println("TURN_LEFT_LINE");
delay(100);
back_before_turn(8);

//advance_before_tll(400); stopp();
delay(300);
int tt = time_turn_l_l[ll]; turn_left_line(tt);
ll++;
}
//closing TURN_LEFT_LINE
break;

//-----------------------
// GO_TO_BIN
//-----------------------
case GO_TO_BIN:
{ //opening GO_TO_BIN
print_state(); // prints the current state to serial port Serial.println("GO_TO_BIN");
go_to_bin();
}

//closing GO_TO_BIN
break;

//-----------------------
// BACK_TO_LINE
//-----------------------
case BACK_TO_LINE:
{ //opening BACK_TO_LINE
print_state(); // prints the current state to serial port Serial.println("BACK_TO_LINE"); back_to_line();
stopp();
delay(1300);
}
//closing BACK_TO_LINE
break;

//-----------------------
//STACK
//-----------------------
case STACK:
{ //opening STACK
print_state(); // prints the current state to serial port Serial.println("STACK");
if(stack == 0)
firstStack();
else if(stack<5)
bstack();
else
lastStack();
}
//closing STACK
break;

//-----------------------
//STOP
//-----------------------

case STOP:
{ //opening STOP
print_state(); // prints the current state to serial port Serial.println("stop");
stopp();
}
//closing STOP
break;

//-----------------------
// ALIGNED
//-----------------------
case aligned:
{

back_before_turn(6);
delay(300);
aligned_bin(millis(),1000);

}
break;
//-----------------------
// default
//-----------------------
default:
{ //opening default
stopp();
}
//closing default
break;

}//closing switch

ii++;
}
// closing loop

Functions

// ================================================================ // Function
// ================================================================ void back_before_turn(long timee);

void turn_180_r_bin (long turntime);

void turn_180_l_bin(long turntime);

void print_state()
{
if (state == STOP)
{
Serial.println("STATE = STOP ###################"); }
else if (state == LINE_FOLLOWING)
{
Serial.println("STATE = LINE_FOLLOWING ###################"); }
else if (state == TURN_LEFT_BIN)
{
Serial.println("STATE = TURN_LEFT_BIN ####################"); }
else if (state == TURN_RIGHT_BIN)
{
Serial.println("STATE = TURN_RIGHT_BIN ###################"); }
else if (state == TURN_LEFT_LINE)
{
Serial.println("STATE = TURN_LEFT_LINE ###################");

}
else if (state == TURN_RIGHT_LINE)
{
Serial.println("STATE = TURN_RIGHT_LINE ##################"); }
else if(state == GO_TO_BIN)
{
Serial.println("STATE = GO_TO_BIN ########################"); }
else if(state == BACK_TO_LINE)
{
Serial.println("STATE = BACK_TO_LINE #####################"); }
else if (state == STACK)
{
Serial.println("STATE = STACK ############################"); }
else if (state == OPPOSITE_R)
{
Serial.println("STATE = OPPOSITE_R ##########################"); }
else if (state == OPPOSITE_L)
{
Serial.println("STATE = OPPOSITE_L ##########################"); }
else if (state == test)
{
Serial.println("STATE = test ##########################"); }
}

int set_state()
{
if (itr_s < num_states_to_do -1) {
itr_s = itr_s +1;
return states_to_do[itr_s];

}

return 0 ;
}
void stopp(void) | //Stop
{
analogWrite(R_ME,0);
digitalWrite(R_M1,LOW);
analogWrite(L_ME,0);
digitalWrite(L_M1,LOW);
}

void advance(char a,char b) //Move forward {

digitalWrite(L_M1,L_Forward);
//delay(1);
digitalWrite(R_M1,R_Forward);
// delay(1);
analogWrite (L_ME,a); //PWM Speed Control //delay(1);
analogWrite (R_ME,b);
delay(1);

}

void read_ir()
{
left_sensor_state | = digitalRead(left_sensor_pin);
right_sensor_state | = digitalRead(right_sensor_pin);
middle_sensor_state | = digitalRead(middle_sensor_pin);
left_arm_sensor_state = digitalRead(left_arm_sensor_pin); right_arm_sensor_state = digitalRead(right_arm_sensor_pin); front_right_sensor_state = digitalRead(front_right_pin); front_left_sensor_state = digitalRead(front_left_pin); low_right_sensor_state = (digitalRead(low_right_pin));

if (low_right_sensor_state == 0) digitalWrite(led_r, HIGH);
else
digitalWrite(led_r, LOW);
low_left_sensor_state = (digitalRead(low_left_pin)); if (low_left_sensor_state == 0)
digitalWrite(led_l, HIGH);
else
digitalWrite(led_l, LOW);
}

void back_off (char a,char b) //Move backward {
analogWrite (R_ME,a);
digitalWrite(R_M1,R_Backward);
analogWrite (L_ME,b);
digitalWrite(L_M1,L_Backward);
}

void turn_L (char a,char b) //Turn Left {
analogWrite (R_ME,a);
digitalWrite(R_M1,R_Forward); analogWrite (L_ME,b);
digitalWrite(L_M1,L_Backward);
}

void turn_L_line (char a) //Turn Left {
analogWrite (R_ME,a);
digitalWrite(R_M1,R_Forward); analogWrite (L_ME,0);
digitalWrite(L_M1,LOW);
}

void turn_R (char a,char b) //Turn Right {

analogWrite (R_ME,a);
digitalWrite(R_M1,R_Backward); analogWrite (L_ME,b);
digitalWrite(L_M1,L_Forward); }

void turn_R_line

(char

b

) //Turn Right
{
analogWrite (R_ME,

0);
digitalWrite(R_M1,LOW);
analogWrite (L_ME,b);
digitalWrite(L_M1,L_Forward); }

void go_straight() {

int temp1 = abs

(cur_wvel

[

1]

- cur_wvel

[

0]);

if (temp1 >= 0.05 && temp1 <= 0.5

)
{
//speed_L =speed_L;
speed_R =speed_R;
}
else if

(cur_wvel

[

1] > cur_wvel

[

0] )
speed_R--

;
//speed_L--

;
else if

(cur_wvel

[

1] < cur_wvel

[

0])
speed_R++;
//speed_L++; }

void go_straight2() {

int temp1 = abs

(cur_wvel

[

1]

- cur_wvel

[

0]);

if (temp1 >= 0.05 && temp1 <= 0.5

)
{

slow_L =slow_L;
}
else if (cur_wvel[1] > cur_wvel[0] ) slow_L--;
else if (cur_wvel[1] < cur_wvel[0]) slow_L++;
}

void fix_turn_r_90_line(int right, int left)
{
read_ir();
while(left_sensor_state != BLACK && middle_sensor_state != BLACK && left_sensor_state != BLACK) {
analogWrite (R_ME,right);
analogWrite (L_ME,left);
digitalWrite(R_M1,R_Forward); digitalWrite(L_M1,L_Backward); read_ir();
}
}

void fix_turn_l_90_line(int right, int left)
{
read_ir();
while(left_sensor_state != BLACK && middle_sensor_state != BLACK && left_sensor_state != BLACK) {

analogWrite (R_ME,right);
analogWrite (L_ME,left);
digitalWrite(R_M1,R_Backward); digitalWrite(L_M1,L_Forward); read_ir();
}
}

void turn_90_r(int right, int left, long time2, int time_to_turn) {

analogWrite (R_ME,right);
analogWrite (L_ME,left);
long TimeMillis = 0;
time2= millis();
int t = 0;
while(TimeMillis - time2< time_to_turn)
{ | //Time to turn towards bin
Serial.println("---------------------Time to turn: "); Serial.println(TimeMillis - time2); digitalWrite(R_M1,R_Forward); digitalWrite(L_M1,L_Backward);
TimeMillis = millis();
t++;
}
analogWrite (R_ME,0);
analogWrite (L_ME, 0);
//fix_turn_r_90_line(right,left);
}

void turn_90_l(int right, int left, long time2, int time_to_turn) {
analogWrite (R_ME,right);
analogWrite (L_ME,left);
long TimeMillis = 0;
time2 = millis();
int t = 0;
while(t< time_to_turn)
{ | //Time to turn towards bin
Serial.println("turn 90 l---------------------Time to turn: "); Serial.println(TimeMillis - time2); digitalWrite(R_M1,R_Backward); digitalWrite(L_M1,L_Forward);
TimeMillis = millis();
t++;
}
analogWrite (R_ME,0);
analogWrite (L_ME, 0);

//fix_turn_l_90_line(right,left); }

void advance_before_tll(long timee)
{
Serial.println("FUNCTION advance_before_tll"); long TimeMillis = 0;

long time = millis();
while(TimeMillis - time < timee) //700)
{ | //Time to turn towards bin
| Serial.println(" advance_before_tll: "); Serial.println(TimeMillis - time);
| get_current_status();
| go_straight(); advance(speed_R,speed_L);
| TimeMillis = millis();
}

}

void aligned_bin(int time1, long correct_time) {

int r = speed_R;
int l = speed_L;
speed_R = speed_R - alignement_factor; speed_L = speed_L - alignement_factor; //int correct_time = 200;
//int time1 = millis();
Serial.println("==========alignee======="); read_ir();

int exit = 0;
long TimeMillis = 0;

int invert = 0;
int forward = 0;
while (exit == 0)
{

Serial.print(front_left_sensor_state); Serial.print("\t");
Serial.print(front_right_sensor_state); Serial.print("\t");
Serial.println(TimeMillis);

if (TimeMillis - time1 < correct_time) invert =1;

read_ir();

//L(B) M(?) R(W)
if (front_left_sensor_state == BLACK && front_right_sensor_state == WHITE )
{
Serial.println("front_left_sensor_state == BLACK && front_right_sensor_state == WHITE"); //back_off(0, turn_speed);
if (invert == 0)
{
advance(turn_speed+7, 0);
Serial.println("advance(0, turn_speed"); }
//advance(0, turn_speed -7);
else
{
back_off(turn_speed+7, 0); // worked Serial.println(" back_off(0,turn_speed);"); }

}

else if (front_left_sensor_state == WHITE && front_right_sensor_state == BLACK )

{
Serial.print(" front_left_sensor_state == WHITE && front_right_sensor_state == BLACK left correction"); //back_off(turn_speed, 0);
if (invert == 0)
{
advance(0, turn_speed+7); // worked = turn_l_line Serial.println(" advance(turn_speed, 0);");
}
//advance (0,turn_speed -7);
else
{
back_off(0,turn_speed+7); // worked Serial.println("back_off(turn_speed, 0);"); }

}
else if(front_left_sensor_state == BLACK && front_right_sensor_state == BLACK) {

/*
if (invert == 1)
{
back_off (turn_speed, turn_speed); Serial.print("bCK");
}
else
{*/
advance(speed_R,speed_L);
Serial.print("advance");
// }
}
else
{
Serial.println("aligned"); stopp();
delay(200);
exit = 1;

}
TimeMillis = millis();
}
speed_R = r;
speed_L = l;
}

void aligned_bin_right(long time1, long correct_time) {
Serial.println("FUNCTION aligned_bin_right");
//int correct_time = 200;
//int time1 = millis();
Serial.println("==========aligned_bin_right======="); read_ir();

int exit = 0;
long TimeMillis = 0;
int invert = 0;
int forward = 0;
while (exit == 0)
{
Serial.print("forward ");
Serial.println(forward);
Serial.print(front_left_sensor_state); Serial.print("\t");
Serial.print(front_right_sensor_state); Serial.print("\t");
Serial.print("front_left_sensor_state "); Serial.println(front_left_sensor_state);

//Serial.println(TimeMillis);

if (TimeMillis - time1 < correct_time) invert =1;

Serial.print("Invert ");
Serial.println(invert);

read_ir();

//L(B) M(?) R(W)
if (front_left_sensor_state == BLACK && front_right_sensor_state == WHITE )
{
//Serial.println("front_left_sensor_state == BLACK && front_right_sensor_state == WHITE"); //back_off(0, turn_speed);
if (invert == 0)
{
//advance(turn_speed+7, 0);
advance(0, turn_speed+15); Serial.println("advance(0, turn_speed+7)"); }
//advance(0, turn_speed -7);
else
{
//back_off(turn_speed+7, 0); // worked back_off(0, turn_speed+10); Serial.println(" back_off(0, turn_speed+7);"); }

}

else if (front_left_sensor_state == WHITE && front_right_sensor_state == BLACK )
{
//Serial.print(" front_left_sensor_state == WHITE && front_right_sensor_state == BLACK left correction"); //back_off(turn_speed, 0);
if (invert == 0)
{
//advance(0, turn_speed+7); // worked = turn_l_line advance(turn_speed+10, 0);
Serial.println(" advance(turn_speed+7, 0)");
}
//advance (0,turn_speed -7);
else

{
//back_off(0,turn_speed+7); // worked back_off(turn_speed+10, 0) ; Serial.println("back_off(turn_speed+7, 0) ;"); }

}
else if(front_left_sensor_state == BLACK && front_right_sensor_state == BLACK) {

if (invert == 0 )
{
back_off (turn_speed, turn_speed);
Serial.println("Invert == 1back_off (turn_speed, turn_speed);"); }
else
{
advance(speed_R,speed_L);
}
}
else
{
Serial.println("aligned"); stopp();
exit = 1;
}
TimeMillis = millis();
}
}

void line_following(int lines, int dir) {
while(white_lines != lines)
{
read_ir();

// LEFT
// | | | |
// | L M R
// | | | |
// <- L
// L(W) M(W) R(B)
if(left_sensor_state == WHITE && middle_sensor_state == WHITE && right_sensor_state == BLACK ) {
Serial.println("LINE FOLLOWING turning left L(W) M(W) R(B) ");
advance(speed_R, speed_L+ plus_factor);
//advance(speed_R + plus_factor , speed_L); Serial.println("advance(speed_R, speed_L+ plus_factor);");

}
else
{ // opening else - right eft - left - stop - forward read_ir();
// RIGHT
// | | | |
// | R
// M | |
// L | | |
//-> R
// L(B) M(B) R(W)
if (left_sensor_state == BLACK && middle_sensor_state == BLACK && right_sensor_state == WHITE ) {
Serial.println("LINE FOLLOWING going right L(B) M(B) R(W)");
advance(speed_R + plus_factor , speed_L);
//advance(speed_R , speed_L + plus_factor); Serial.println("advance(speed_R + plus_factor, speed_L);");
}
else
{// opening else - left - left - stop - forward
read_ir();
// RIGHT
// ||||
// L M R

// ||||
// L(B) M(W) R(W)
// ->R
if(left_sensor_state == BLACK && middle_sensor_state == WHITE && right_sensor_state == WHITE ) {// opening if - go right
Serial.println("LINE FOLLOWING going left L(B) M(W) R(W)");
//advance(speed_R +8, speed_L );

// advance(speed_R , speed_L + plus_factor ); advance(speed_R + plus_factor, speed_L);

//advance(speed_R + plus_factor , speed_L); Serial.println(" advance(speed_R , speed_L + plus_factor);");

}// close if - go left
else
{ // opening else - left - stop - forward read_ir();
// LEFT
// L(W) M(B) R(B)
// | | | |
// | L
// | | | M
// | | | R
// <-
if (left_sensor_state == WHITE && middle_sensor_state == BLACK && right_sensor_state == BLACK ) { // opening if - going left
Serial.println("LINE FOLLOWING turning right L(W) M(B) R(B) ");
| advance(speed_R , speed_L + plus_factor);
| //advance(speed_R + plus_factor, speed_L );
| Serial.println("advance(speed_R , speed_L + plus_factor);");

} // closing if - going left
else
{ // opening else - stop & forward

read_ir();
// STOP
if(left_sensor_state == WHITE && middle_sensor_state == WHITE && right_sensor_state == WHITE) { // opening if - stop
if (white_lines == lines)
{ // opening if - stop
Serial.println("LINE FOLLOWING stop | = | = | = = | = | = | = | = | = =");
stopp();

//state = TURN_TO_BIN;
} // closing if - stop
else
{ // opening else - pass white line
while(left_sensor_state == WHITE && middle_sensor_state == WHITE && right_sensor_state == WHITE) { // opening while loop - pass white line
read_ir();
Serial.print("|||||||||||||||| PASSING WHITE|||||||||||||||||| ");
Serial.println(white_lines);
get_current_status(); // get velocity

advance(speed_R,speed_L); // move forward go_straight(); // correct velocity e_turn =0;
} // closing while loop - pass white line white_lines++;
// state++;
} // close else - pass white line
} // closing if - stop
else
{ //opening else - froward
read_ir();
// FORWARD
if(left_sensor_state == BLACK && middle_sensor_state == WHITE && right_sensor_state == BLACK) // ASK ISA
{ // opening if - forward
Serial.println("LINE FOLLOWING: going forward");
get_current_status(); // get velocity

// Serial.println(speed_L);
// Serial.print("\t");
// Serial.print(speed_R);
advance(speed_R,speed_L); | // advance
go_straight(); | // correct velocity
e_turn =0;
} // closing if - forward
} //closing else - froward
} // closing else - stop & forward
} // closing else - left - stop - forward
}// closing else - left - left - stop - forward }// closing else - right eft - left - stop - forward }

if (dir == plus_dir)
pos = pos + white_lines;
else if (dir == minus_dir) pos = pos - white_lines;

white_lines = 0;
}

void back_to_line_front()
{
Serial.println("BACK TO LINE FRONT");

int r = speed_R;
int l = speed_L;
speed_R = speed_R -15;
speed_L = speed_L - 7;
int l1_r2= 0;
int r1_l2 = 0;
read_ir();

long TimeMillis = 0;
int correct = 0;
long time1 = millis();

while((front_left_sensor_state == BLACK || front_right_sensor_state == BLACK) && correct == 0 ) { //Time to turn backwards bin

/*if (front_left_sensor_state == WHITE )
{
Serial.print("l1_r2 ");
Serial.println(l1_r2);
l1_r2 = 1;
}
if(front_right_sensor_state == WHITE ) {
Serial.print("r1_l2 ");
Serial.println(r1_l2);
r1_l2 = 1;
}

if (l1_r2 == 1 && front_right_sensor_state == WHITE) {
l1_r2 = 2;
Serial.print("l1_r2 ");
Serial.println(l1_r2);
}

if (r1_l2 == 1 && front_left_sensor_state == WHITE) {
Serial.print("r1_l2 ");
Serial.println(r1_l2);
r1_l2 = 2;
}*/
if ( TimeMillis - time1 < 1300) {
get_current_status();
back_off(speed_R,speed_L); go_straight();

read_ir();
TimeMillis = millis();

Serial.print("SPEED_back_to_line_front"); Serial.println(TimeMillis - time1); Serial.println(" back");

}
else
{
get_current_status();
advance(speed_R,speed_L);
go_straight();
read_ir();
TimeMillis = millis();

Serial.println("SPEED_back_to_line_front "); Serial.println(TimeMillis - time1);
Serial.println(" advance");

if (front_left_sensor_state == BLACK || front_right_sensor_state == BLACK) correct = 1;
}

}
get_current_status();
// back_off(speed_R,speed_L); go_straight();
speed_R = r;
speed_L= l;

}

void turn_left_bin(int turntime)

{
turn_90_l(speed_R,speed_R, millis(), turntime); delay(1000);
read_ir();

// back_to_line_front();
back_before_turn(9);
aligned_bin(millis(),1000); }

void turn_right_line(long max) {
analogWrite (R_ME,speed_R); analogWrite (L_ME,speed_L); long TimeMillis = 0;
long correct = 0;
long time1 = millis();
int i = 0;
while(i < 18)
{ | //Time to turn towards bin
Serial.println("turn_right_line ---------------------Time to turn: "); Serial.println(TimeMillis - time1); digitalWrite(R_M1,R_Backward); digitalWrite(L_M1,L_Forward);

i++;
}
analogWrite (R_ME,0);
analogWrite (L_ME, 0);
}

void turn_left_line( int turntime)
{
Serial.println("FUNCTION turn_left_line"); analogWrite (R_ME,speed_R+10); analogWrite (L_ME,speed_L);
unsigned int TimeMillis = 0;

unsigned int time1 = millis(); unsigned int correct = time1; long i = 0;
while(i < turntime)
{ | //Time to turn towards bin
Serial.println("turn_left_line ---------------------Time to turn: "); Serial.println(TimeMillis - time1); digitalWrite(R_M1,R_Forward); digitalWrite(L_M1,L_Backward);
//TimeMillis = millis();

i++;
}

/*
if(correct == 2)
{
read_ir();
while (front_left_sensor_state == BLACK) {
| digitalWrite(R_M1,R_Backward);
| digitalWrite(L_M1,L_Forward);
read_ir();
}
| analogWrite (R_ME,0);
analogWrite (L_ME, 0);

}
*/
analogWrite (R_ME,0);
analogWrite (L_ME, 0);
}

void back_to_line()
{

Serial.println("BACK TO LINE");

int r = speed_R;
int l = speed_L;
speed_R = speed_R - 9;
speed_L = speed_L - 6;

read_ir();
while(left_sensor_state == BLACK || right_sensor_state == BLACK) { //Time to turn backwards bin
get_current_status();
back_off(speed_R,speed_L);
go_straight();
read_ir();

Serial.print("SPEED_back_to_line "); Serial.print(speed_L);
Serial.print("\t");
Serial.println(speed_R);
}

/*while(left_sensor_state != WHITE && middle_sensor_state != WHITE && right_sensor_state != WHITE ) { //Time to turn backwards bin
get_current_status();
read_ir();
back_off(speed_L,speed_R); go_straight();
// read_ir();
}*/
speed_R =r;
speed_L = l;
}

void turn_right_bin(int turntime) {
Serial.print("turn_right_bin(");

turn_90_r(speed_R,speed_R, millis(), turntime); delay(100);

back_before_turn(9);
delay(300);

//aligned_bin_right(millis(),1000); aligned_bin(millis(),1000);
}

void back_before_turn(long timee)
{
Serial.println("FUNCTION Back before turn"); print_state();
if (state != test && state != OPPOSITE_R ){ long TimeMillis = 0;
int t = 0;
long time = millis();
while(t < timee) //700)
{ | //Time to turn towards bin Serial.println(" back_before_turn() ---------------------backwardsn: ");
| Serial.println(TimeMillis - time);
| back_off(speed_R,speed_L); get_current_status();
| go_straight();

// TimeMillis = millis();
t++;
}
}
else
{
turn_180_l_bin(2200);
}
}

void turn_180_r_bin( long turntime)
{
Serial.println("FUNCTION turn_180_r_bin"); print_state();

int right = speed_R;
int left = speed_R;

analogWrite (R_ME,right);
analogWrite (L_ME,left);
long TimeMillis = 0;
long time2 = micros();
Serial.println(TimeMillis); Serial.println(time2);
Serial.println(turntime);
Serial.println(TimeMillis - time2);

while(TimeMillis - time2 < turntime)
{ | //Time to turn towards bin
Serial.println("---------------------Time to turn: "); Serial.println(TimeMillis - time2); digitalWrite(R_M1,R_Forward); digitalWrite(L_M1,L_Backward);
TimeMillis = micros();
}
analogWrite (R_ME,0);
analogWrite (L_ME, 0);

}

void turn_180_l_bin(long turntime)
{
Serial.println("FUNCTION turn_180_l_bin"); print_state();

int right = speed_R;
int left = speed_R;
analogWrite (R_ME,right);
analogWrite (L_ME,left);
long TimeMillis = 0;
long time2 = millis();

while(TimeMillis - time2 < turntime)
{ | //Time to turn towards bin
Serial.println("---------------------Time to turn: "); Serial.println(TimeMillis - time2); digitalWrite(R_M1,R_Backward); digitalWrite(L_M1,L_Forward);
TimeMillis = millis();
}
analogWrite (R_ME,0);
analogWrite (L_ME, 0);

}

void go_to_bin()
{
Serial.println("GO TO BIN FUNCTION"); int exit = 0;
int r = speed_R;
int l = speed_L;
speed_R = speed_R - go_to_factor; speed_L = speed_L - go_to_factor ;

/*
int TimeMillis = 0;
int correct = 0;
int time1 = millis();
while(TimeMillis - time1 < 1500)

{ | //Time to turn towards bin
Serial.println("Arbitrary time going forward to avoid line detection: "); Serial.println(TimeMillis - time1);
advance(speed_R, speed_L);
TimeMillis = millis();
read_ir();
}
*/

while (exit == 0)
{
| Serial.print("front_right_sensor_state ");
| Serial.println(front_right_sensor_state);
read_ir();
if (
| ((left_arm_sensor_state == WHITE && right_arm_sensor_state == WHITE ) && (low_right_sensor_state ==
WHITE ) || (low_right_sensor_state == WHITE ))
| || (low_right_sensor_state == WHITE ) || (low_right_sensor_state == WHITE ))
{
| Serial.print(left_arm_sensor_state); Serial.print("\t");
| Serial.print(right_arm_sensor_state);
| Serial.print("\t");
| Serial.print(low_left_sensor_state); Serial.print("\t");
| Serial.println(low_right_sensor_state);

stopp();
exit = 1;
}
| else if (left_arm_sensor_state == WHITE && right_arm_sensor_state == BLACK)
{
| Serial.print("left arm");
| turn_R_line(turn_speed+5);
}
| else if(left_arm_sensor_state == BLACK && right_arm_sensor_state == WHITE)
{

turn_L_line(turn_speed+6);

}
else
{
Serial.println("Forward"); get_current_status();
go_straight();
advance(speed_R,speed_L); // move forward }
}

speed_R = r;
speed_L = l;
}

void back_off_time(long time_t)
{
Serial.println("FUNCTION back_off_time"); long TimeMillis = 0;
long time1 = micros();
while(TimeMillis - time1 < time_t)
{
Serial.print("Timemillis "); Serial.println(TimeMillis); Serial.print("Time1 ");
Serial.println(time1);
Serial.println(TimeMillis - time1 ); Serial.println("back off to turn"); back_off(speed_L-15,speed_R-15); TimeMillis = micros();

}
}

int d2s(long block, int dir)

{ // opening d2s
//This function converts the block height to a number of // steps for the stepper to take.
// block is the desired travel distance for the claw
// dir is the desired direction of travel; 1 to move up // and -1 to move down.
int steps = 0;
steps = -dir*block*19.2*200/8;
pos_claw += block*dir;
Serial.print(pos_claw);
return steps;
}
// closing d2s

void firstStack()
{ // opening firstStack
servo_bot.write(bclose);
servo_top.write(tclose);
delay(500);
servo_top.write(90);
servo_bot.write(bopen);
myStepper.step(d2s(3,up)); stack+=1;
}
// closing firstStack

void lastStack()
{ // opening lastStack
servo_bot.write(bclose);
servo_top.write(tclose);
delay(500);
myStepper.step(d2s(stack,down)); }
// closing lastStack

void bstack()
{ // opening bstack

stack+=1;
Serial.print("\n Stacking");
// Close bottom claw on block servo_bot.write(bclose);
delay(1000);

// Actively close on block Serial.print("\n Closing Top"); servo_top.write(tclose);
delay(500);

// Lower Stepper to place stack on block Serial.print("\n Moving Down"); myStepper.step(d2s(pos_claw-stack+1.4,down)); delay(1500);

//open top claw
Serial.print("\n Opening Claw"); servo_top.write(topen);
delay(1500);
servo_top.write(90);
delay(500);

// Move top Claw above stack Serial.print("\n Moving Up"); myStepper.step(d2s(stack+1-pos_claw,up)); delay(1500);

// Close top claw
Serial.print("\n Closing Claw"); servo_top.write(tclose);
delay(500);
servo_top.write(90);

// push down stack from top Serial.print("\n Moving Down"); myStepper.step(d2s(pos_claw-stack,down));

delay(1500);
myStepper.step(d2s(stack/2,up));

// open top claw
Serial.print("\n Open Claw"); servo_top.write(topen);
delay(1000);
servo_top.write(90);

// Reposition top claw to above cg of stack Serial.print("\n Moving Down"); myStepper.step(d2s(pos_claw-(stack/2),down)); delay(1500);

// Close top claw
Serial.print("\n Closing Claw"); servo_top.write(tclose);
delay(500);
servo_top.write(90);

// open bottom claw
servo_bot.write(bclose);

// Raise stack above bottom claw Serial.print("\n Moving Up"); myStepper.step(d2s(pos_claw+1,up)); delay(1500);
}

Operation instructions

1. Alter code to desired performance requirements.

2. Upload code to Arduino Mega 2560.
3. Ensure all wires are properly connected using the wiring diagram.
4. Ensure batteries are fully charged and connected.
5. Place Ezio in the white starting square of the playfield.
6. Flip the switch to ensure power is running through entire system.
7. Cease interaction until the product completes its task.
8. If Ezio performs unexpected actions, flip the switch to stop motion and proceed to

troubleshooting.

Maintenance

After each run the ball caster should be cleaned of any debris that may have accumulated.

The sensors should be inspected before each run to ensure there are no obstructions. The

Arduino should be reset periodically to clear the memory. Check wires and connections

periodically for signs of burning or other wear.

Troubleshooting

Problem | Possible Solution
No movement occurs after flipping the switch | Ensure 12V and 9V batteries are fully charged and properly connected.

Ensure Arduino and motor controllers are properly grounded.
Upper/Lower claw does not open/close properly

Check code for possible mistakes. Ensure gear teeth are properly meshed. Robot is not line following properly/ veers off given path

Ensure IR sensors are properly connected. Indicator lights should illuminate when the sensor senses a change in color.
Ensure IR sensors are parallel with the floor.
Buzzing sound coming from either of the two DC motors | Increase the speed of motors in the code
Stepper Motor with lead screw doesn’t turn despite correct connections | Flip 1A and 1B wires going to stepper motor connections
No Robot movement and IR sensors are off after flipping the power switch | Ensure that no metal parts are touching IR sensor connections.

| Check if the buck converter light is lit. If light is off, ensure that the battery is plugged. If buck converter light is not lit after plugging battery, change the buck converter.
Robot doesn’t go towards the bins after turning from the center line | Check that one of the bottom IR sensors is not stuck in the Active state.
There is smoke or burning components coming from the robot | Safely unplug the batteries and check connections according to the wiring diagram.
Arduino doesn’t successfully upload new code | Disconnect the batteries or any power connections and try to upload the code again.
The DC motor battery is connected but the power switch remains off when switched. | Check the battery fuse holder, and replace any blown fuses. Refer to the wiring diagram for proper connections.

Drawings

Note: All drawing dimensions are in US units, except for the gears on the claws, which

are metric. All holes are 3mm, or 1/8" unless otherwise specified.

Upper Base

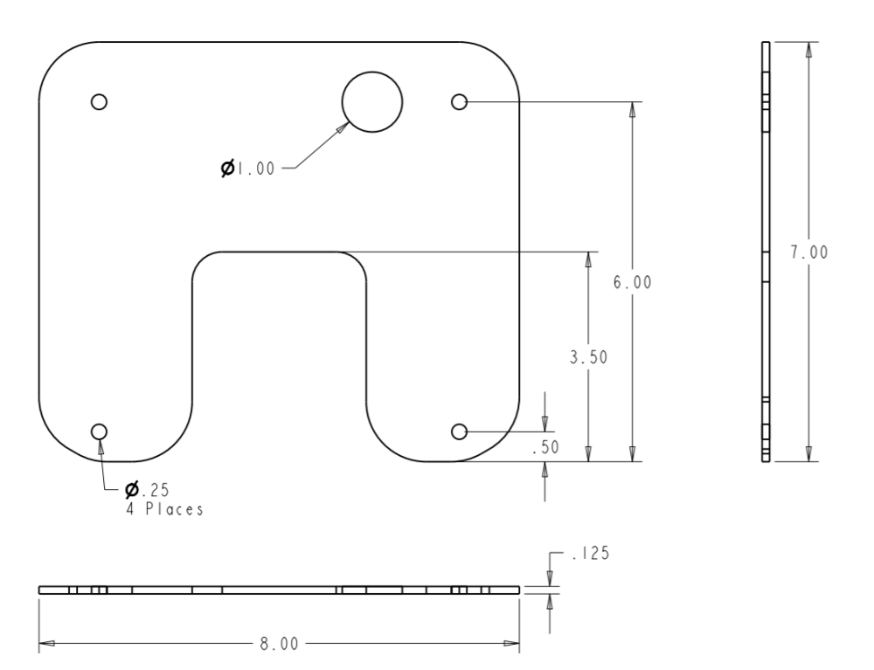
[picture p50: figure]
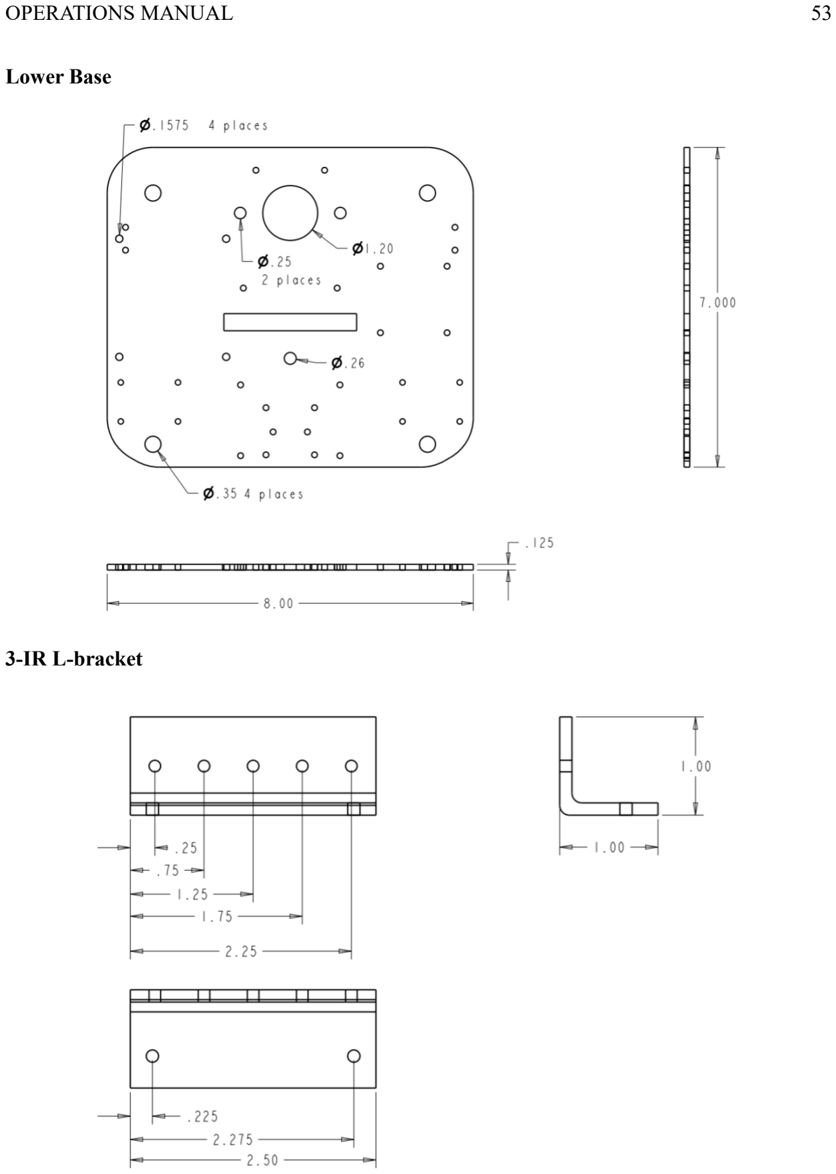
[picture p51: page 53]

Lower Base

3-IR L-bracket

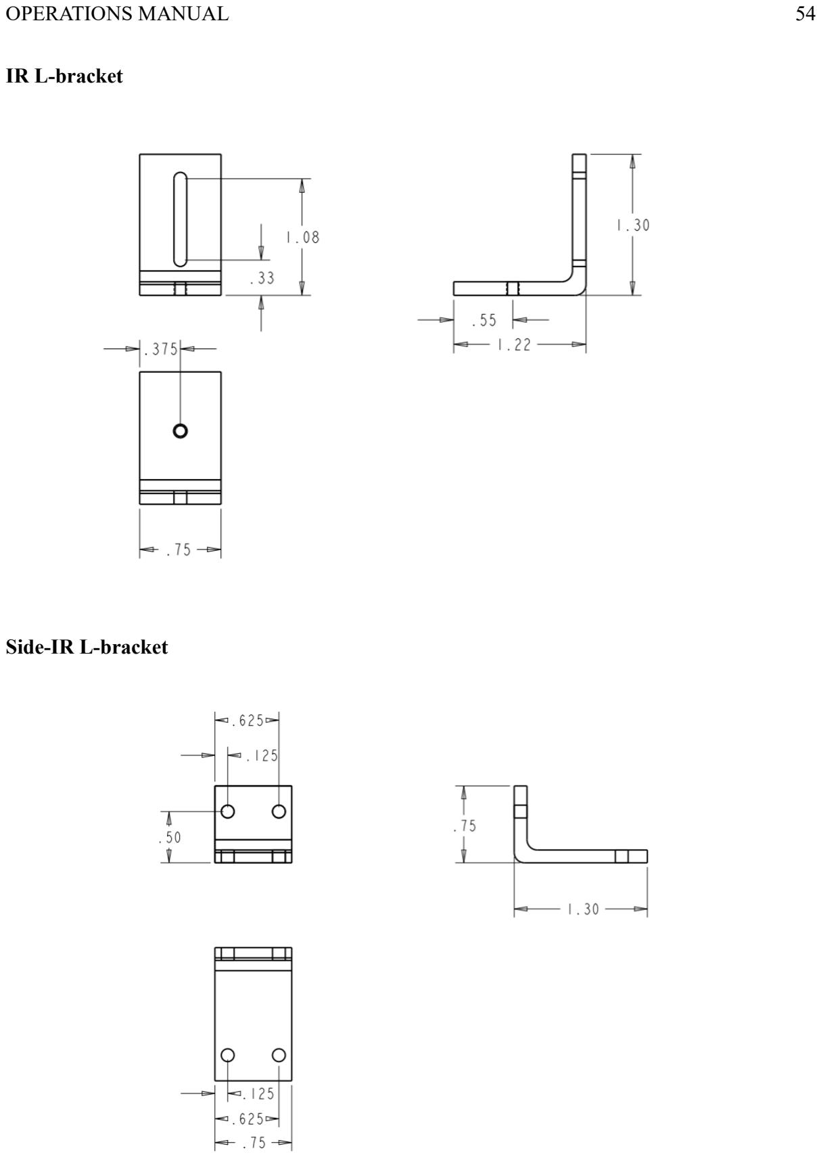
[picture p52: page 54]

IR L-bracket

Side-IR L-bracket

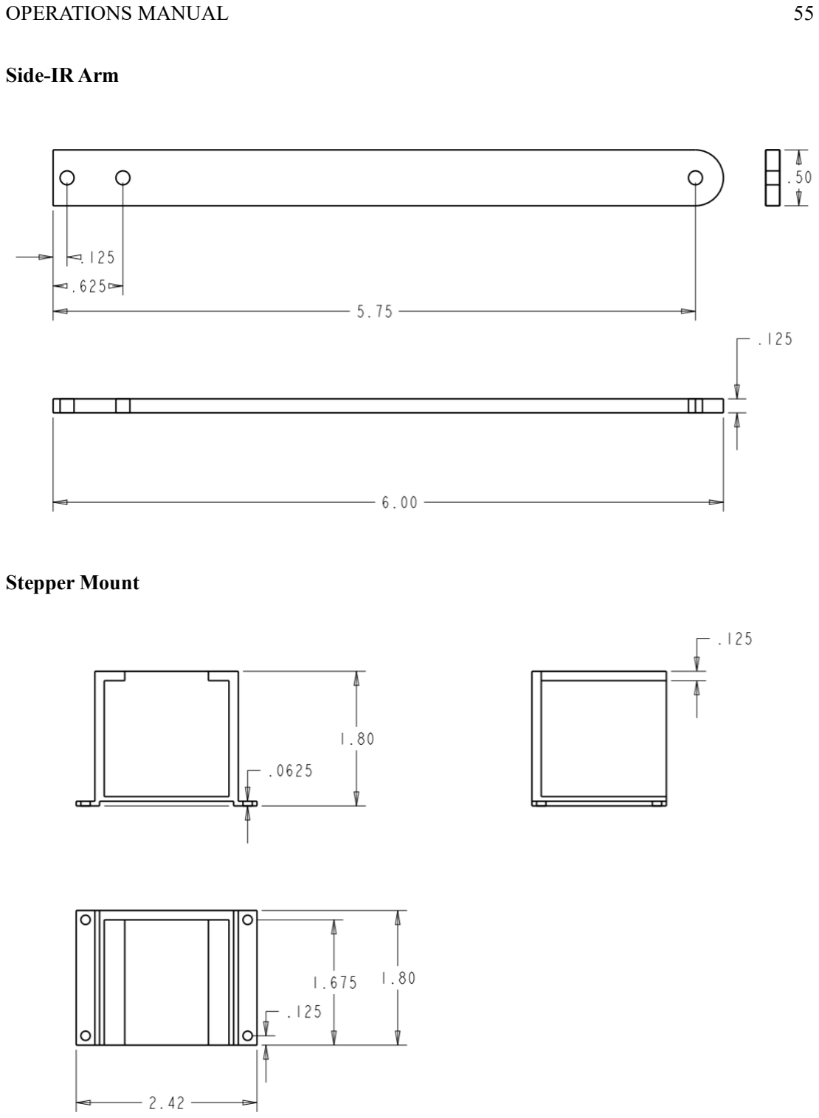
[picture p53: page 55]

Side-IR Arm

Stepper Mount

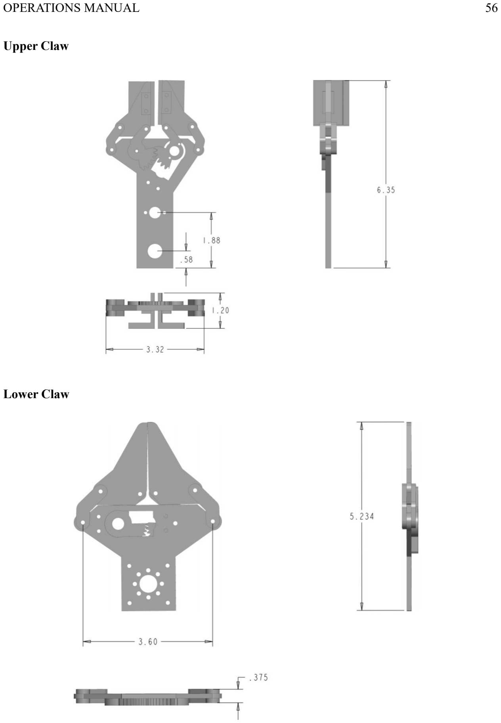
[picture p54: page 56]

Upper Claw

Lower Claw

Endzone Base

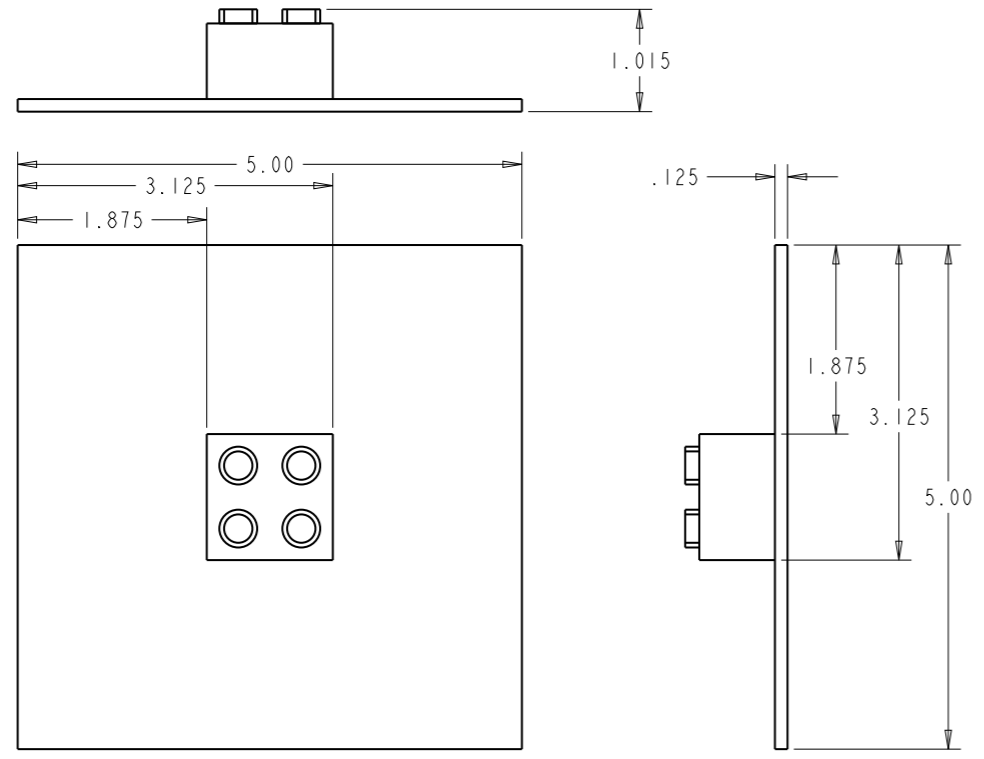
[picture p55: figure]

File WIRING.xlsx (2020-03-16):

 | MODULE |  | HARDWARE NAME | COLOR | PIN | VARIABLE NAME | WIRE LABEL +/- | WIRE LABEL
DC MOTORS | 1 | RIGHT | M1_PWM | ORANGE | 3 | R_ME |  | DMMD
 |  |  | M1_EN | YELLOW | 23 | R_M1
 |  | LEFT | M2_PWM | GREEN | 2 | L_ME
 |  |  | M2_EN | BLUE | 22 | L_M1
 |  | VCC | * | RED | * | * | DC +
 |  | GND | * | BLACK | * | * | DC -
DC MOTORS ENCODERS | R | RIGHT | MOTOR POWER 5V | RED | * | * |  | R
 |  |  | MOTOR POWER GND | BLACK | * | *
 |  |  | ENCODER GND | GREEN | * | * | RE-
 |  |  | ENCODER VCC | BLUE | * | * | RE+
 |  |  | ENCODER A | YELLOW | 26 | interruptPIN2
 |  |  | ENCODER B | WHITE | 27 | interruptPIN3
 | L | LEFT | MOTOR POWER 5V | RED | * | * |  | L
 |  |  | MOTOR POWER GND | BLACK | * | *
 |  |  | ENCODER GND | GREEN | * | * | LE+
 |  |  | ENCODER VCC | BLUE | * | * | LE-
 |  |  | ENCODER A | YELLOW | 24 | interruptPIN0
 |  |  | ENCODER B | WHITE | 25 | interruptPIN1
IR | LF | RIGHT | IR | ORANGE | 10 | right_sensor_pin |  | LF
 |  |  |  | RED |  |  | RLF+
 |  |  |  | BLACK |  |  | RLF-
 |  | LEFT | IR | BLUE | 11 | left_sensor_pin
 |  |  |  | RED |  |  | LLF+
 |  |  |  | BLACK |  |  | LLF-
 |  | MIDDLE | IR | WHITE | 12 | middle_sensor_pin
 |  |  |  | RED |  |  | MLF+
 |  |  |  | BLACK |  |  | MLF-
 | ARM | RIGHT | IR | BLUE | 28 | right_arm_sensor_pin |  | RAIR
 |  |  |  | RED |  |  | RA+
 |  |  |  | BLACK |  |  | RA-
 |  | LEFT | IR | GREEN | 13 | left_arm_sensor_pin |  | LAIR
 |  |  |  | RED |  |  | LA+
 |  |  |  | BLACK |  |  | LA-
 | FRONT | RIGHT | IR | GREEN | 29 | front_right_pin |  | RFIR
 |  |  |  | RED |  |  | RF+
 |  |  |  | BLACK |  |  | RF-
 |  | LEFT | IR | YELLOW | 30 | front_left_pin |  | LFIR
 |  |  |  | RED |  |  | LF+
 |  |  |  | BLACK |  |  | LF-
 | LOW | RIGHT | IR | BLUE | 31 | low_right_pin |  | BRIR
 |  |  |  | RED |  |  | RB+
 |  |  |  | BLACK |  |  | RB-
 |  | LEFT | IR |  | 32 | low_LEFT_pin |  | BLIR
 |  |  |  | RED |  |  | LB+
 |  |  |  | BLACK |  |  | LB-
STEPPER |  | RIGHT_STEPPER |  | GREEN | 4 | r_stepper
 |  | LEFT_STEPPER |  | BLUE | 5 | l_stepper
 | stepper |  |  | ORANGE | 6 | myStepper
 |  |  |  | PURPLE | 7

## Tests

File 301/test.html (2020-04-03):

# Project

### Mechanical, Electrical and Software Overview

### Design Summary

## Mechanical, Electrical and Software Design

### Ezio

Ezio
Ezio, is team's 301 automated robot design to complete challenge 1 for the Southeastcon-2020 Hardware Competition. It's name was inspired by the microcontroller that dicatates it's every move, the popular Italian Arduino Mega 2560. Ezio's strategy is to stack the Lego Duplo Blocks from the bottom.

Ezio will travel the Southeastcon hardware competition in a reverse Pi Order. The robot counts with nine Infra-Red, and two low power DC motors in order to navigate through the playfield. Tp pick up the Lego Blocks Ezio counts with a Lead Screw powered by a stepper, as well as two servo motors attached to a geared claw mechanism. The combination of these two system modules, allow Ezio to complete the 1st competition challenge in a simple but efficent way.

### Wiring Diagram

##### Electrical system wiring diagram.

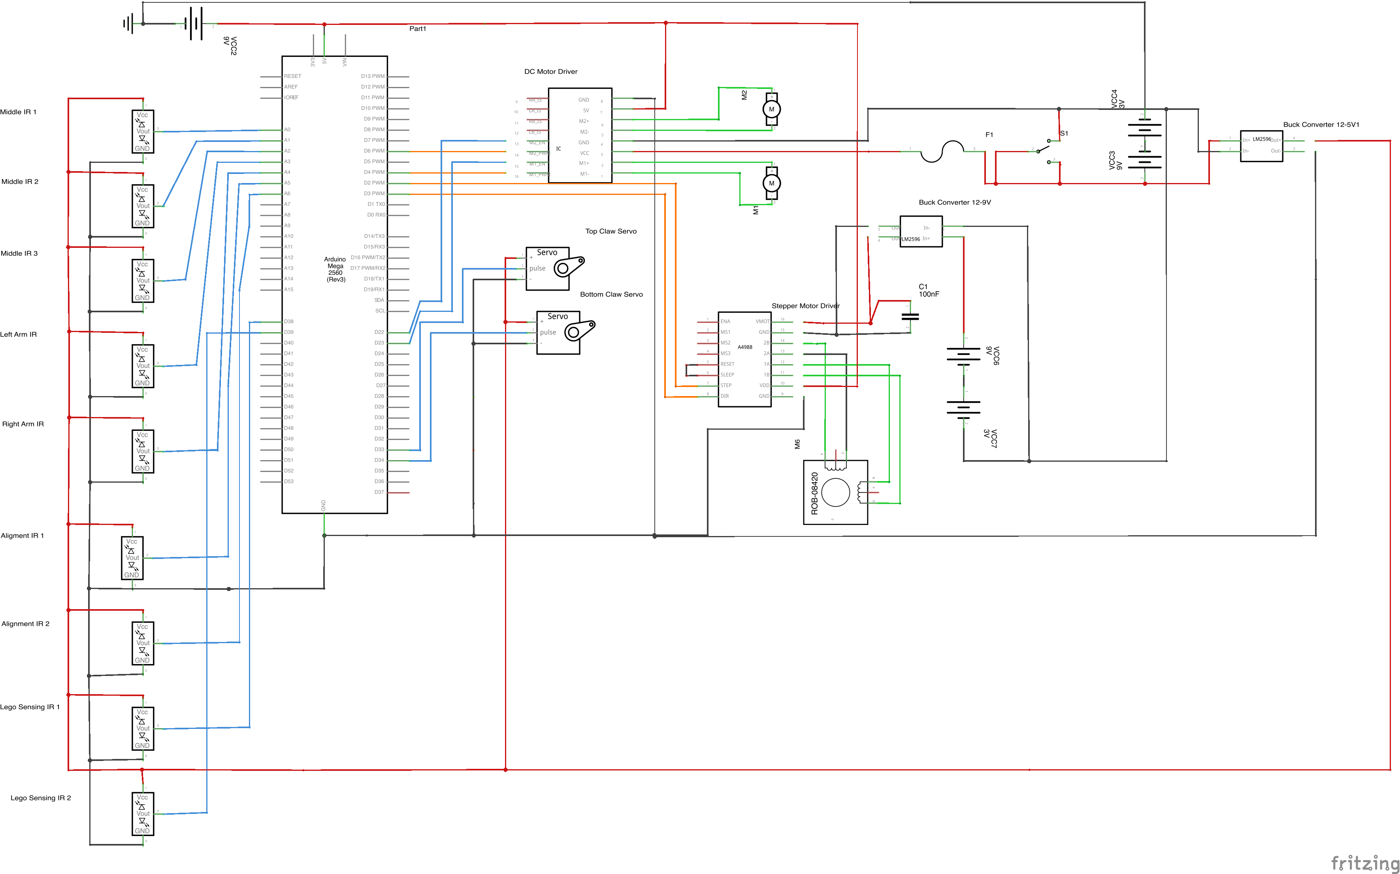
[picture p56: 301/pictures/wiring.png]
Wiring


### Software Diagram

The software was designed to resemble a Finite State Machine. The tasks needed to do by Ezio were separated into modules, or states. Depending on the amount of blocks stacked, Ezio will use one state or another in order to finish the task. Each state contains multiple functions in order to modularize the software's implementation. This type of desing allows for easier implemenation and testing as the project progresses.

Software

COE Logo

Department of Mechanical Engineering

Department of Electrical & Computer Engineering

Website designed by Isabel Barnola
Florida State University
Tallahassee, Florida - 2020

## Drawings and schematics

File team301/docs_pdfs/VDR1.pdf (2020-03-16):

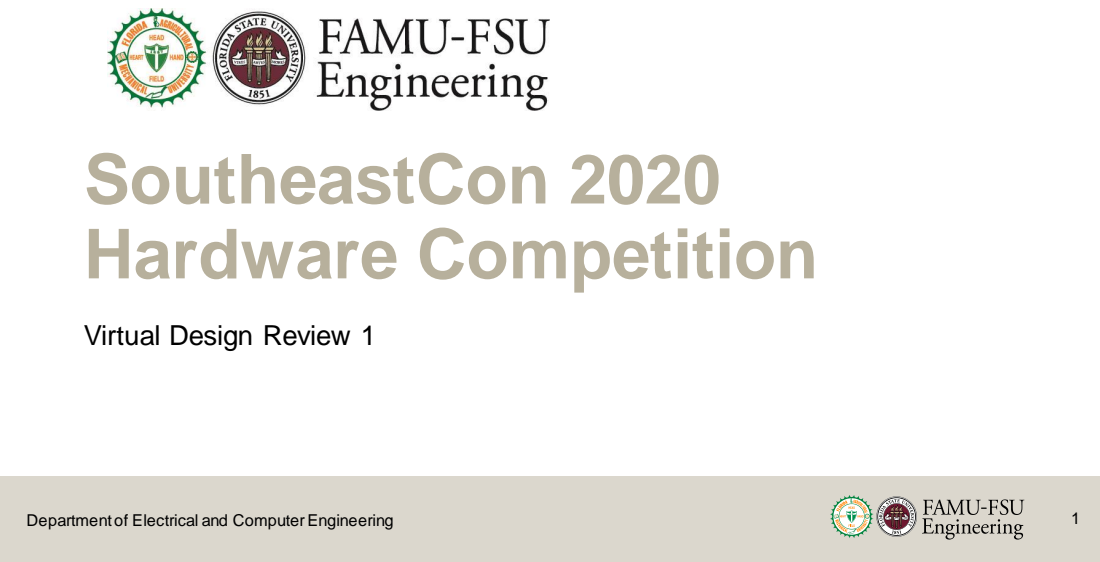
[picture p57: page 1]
SoutheastCon 2020 Hardware Competition

Virtual Design Review 1

Department of Electrical and Computer Engineering

## Team Introductions

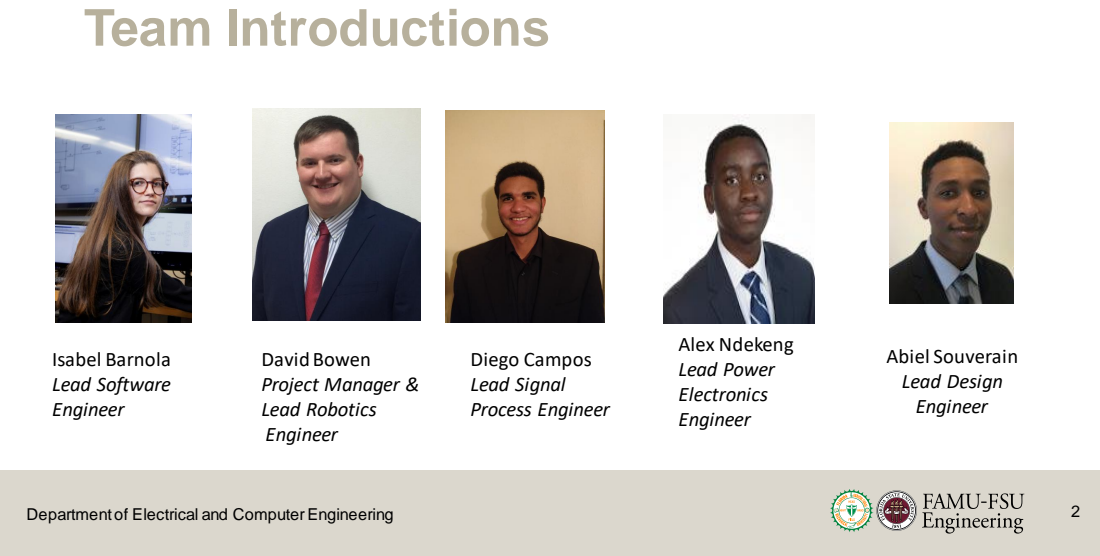
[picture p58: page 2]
Diego Campos Lead Signal Process Engineer; Isabel Barnola Lead Software Engineer; David Bowen Project Manager & Lead Robotics Engineer; Alex Ndekeng Lead Power Electronics Engineer; Abiel Souverain Lead Design Engineer

## Sponsor and Advisor

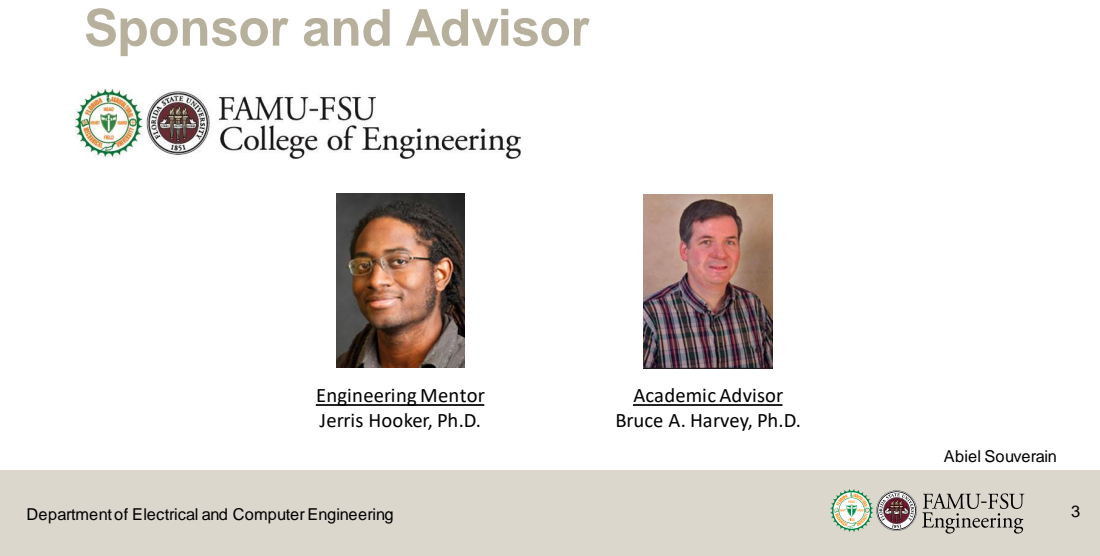
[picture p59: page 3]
Abiel Souverain

Engineering Mentor
Jerris Hooker, Ph.D.

Academic Advisor
Bruce A. Harvey, Ph.D.

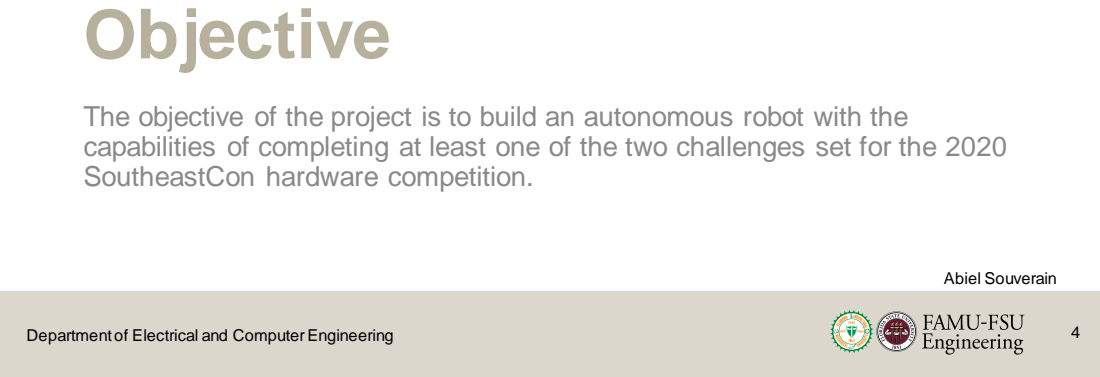
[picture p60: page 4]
Objective; Abiel Souverain

The objective of the project is to build an autonomous robot with the
capabilities of completing at least one of the two challenges set for the 2020
SoutheastCon hardware competition.

## Project Background

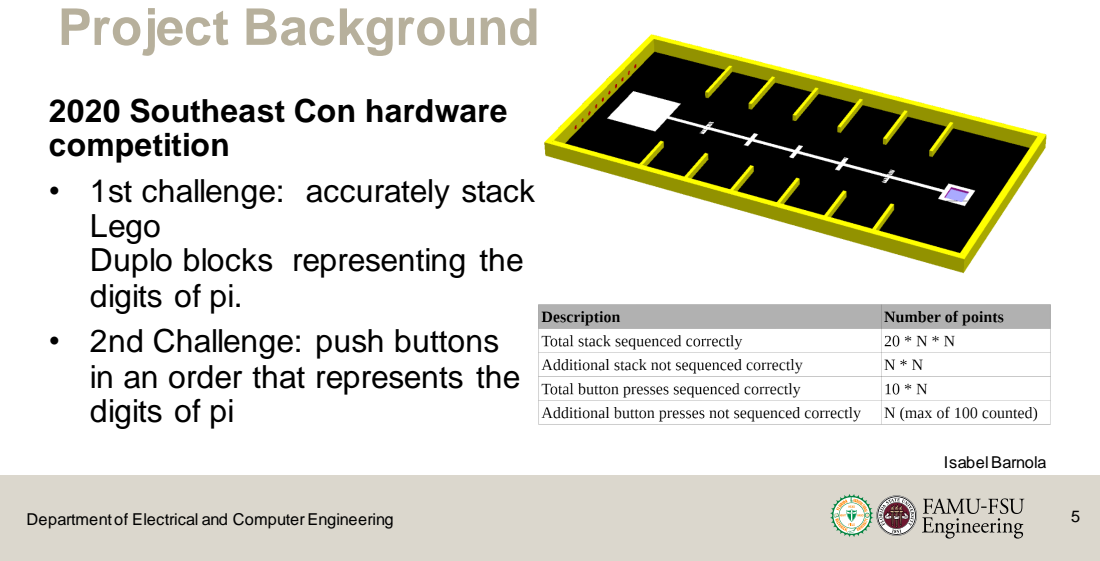
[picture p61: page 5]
Isabel Barnola

2020 Southeast Con hardware
competition • 1st challenge: accurately stack

Lego
Duplo blocks representing the
digits of pi.
• 2nd Challenge: push buttons
in an order that represents the
digits of pi

## Project Scope

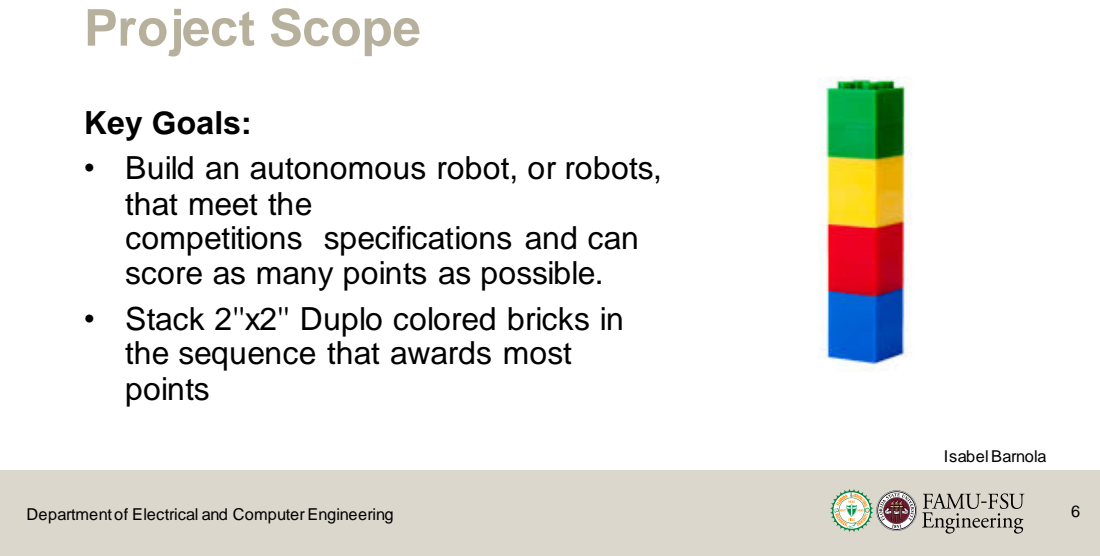
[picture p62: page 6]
Isabel Barnola

Key Goals:
• Build an autonomous robot, or robots,
that meet the
competitions specifications and can
score as many points as possible.
• Stack 2''x2'' Duplo colored bricks in
the sequence that awards most
points

## Project Scope

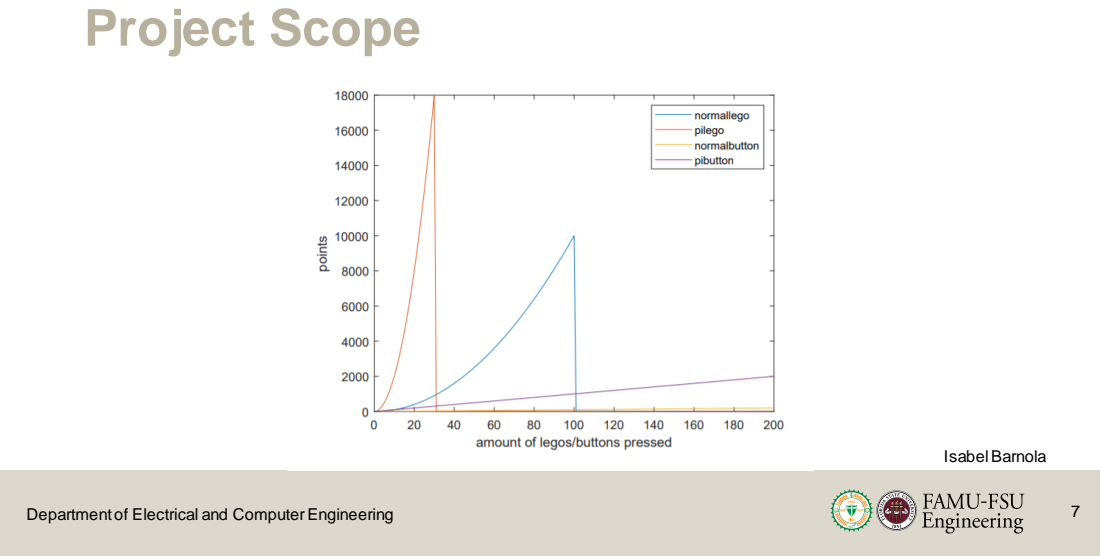
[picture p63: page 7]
Isabel Barnola

## Project Scope

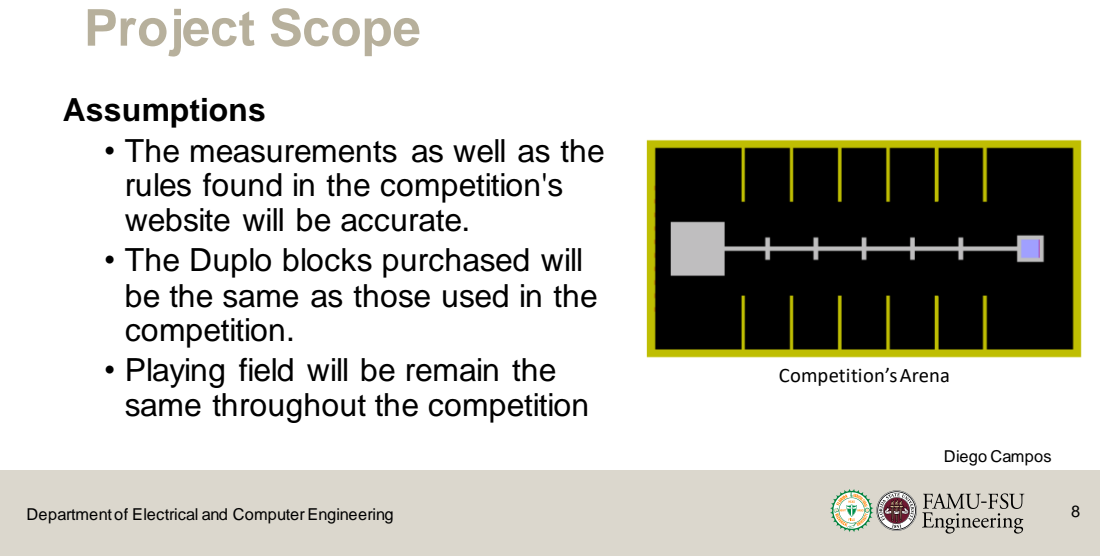
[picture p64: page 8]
Diego Campos; Competition’s Arena

Assumptions
• The measurements as well as the
rules found in the competition's
website will be accurate.
• The Duplo blocks purchased will
be the same as those used in the
competition.
• Playing field will be remain the
same throughout the competition

## Customer Needs

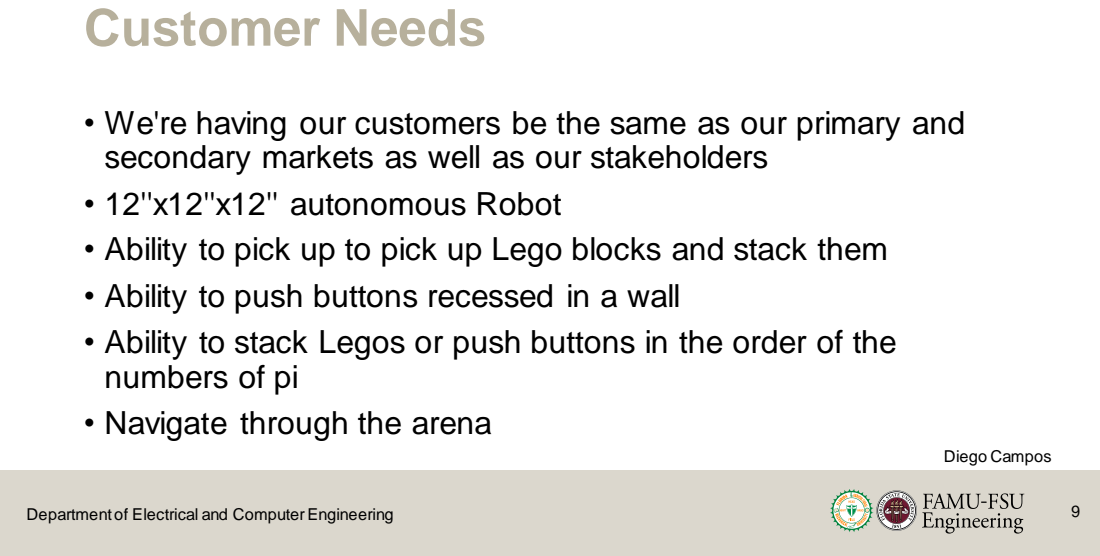
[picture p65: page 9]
Diego Campos

• We're having our customers be the same as our primary and
secondary markets as well as our stakeholders
• 12''x12''x12'' autonomous Robot
• Ability to pick up to pick up Lego blocks and stack them
• Ability to push buttons recessed in a wall
• Ability to stack Legos or push buttons in the order of the
numbers of pi
• Navigate through the arena

## Customer Needs

| Dr. Harvey | Dr. Hooker | Total(Lower is better)
Mobility | 1 | 6 | 7
Accurate Stacking | 4 | 1 | 5
Accurate Button Pushing | 5 | 2 | 7
Stacking | 2 | 3 | 5
Button Pushing | 3 | 4 | 7
Color Recognition | 8 | 5 | 13
Speed | 7 | 7 | 14
Automatic Shutdown | 6 | 8 | 14
Table from surveys given to Dr. Harvey, Dr. Hooker, and Dr. McConomy
- We can see the most important thing is to be able to stack the Legos and do it accurately
- The second most important thing is to be able to push buttons and do it accurately as well as have good

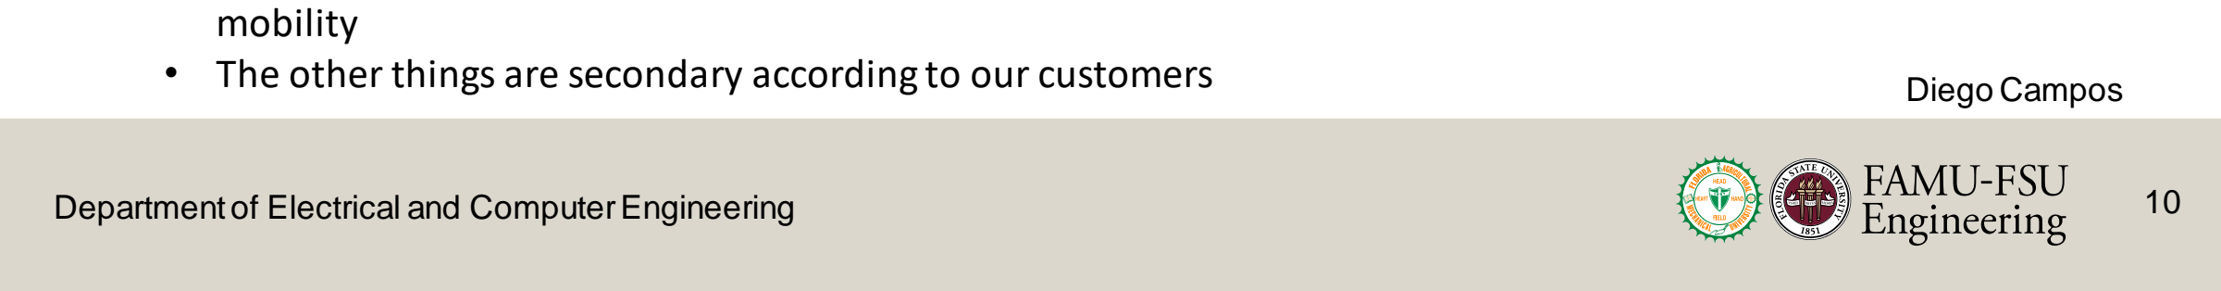
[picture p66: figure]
Diego Campos; mobility

- The other things are secondary according to our customers

## Functional Decomp

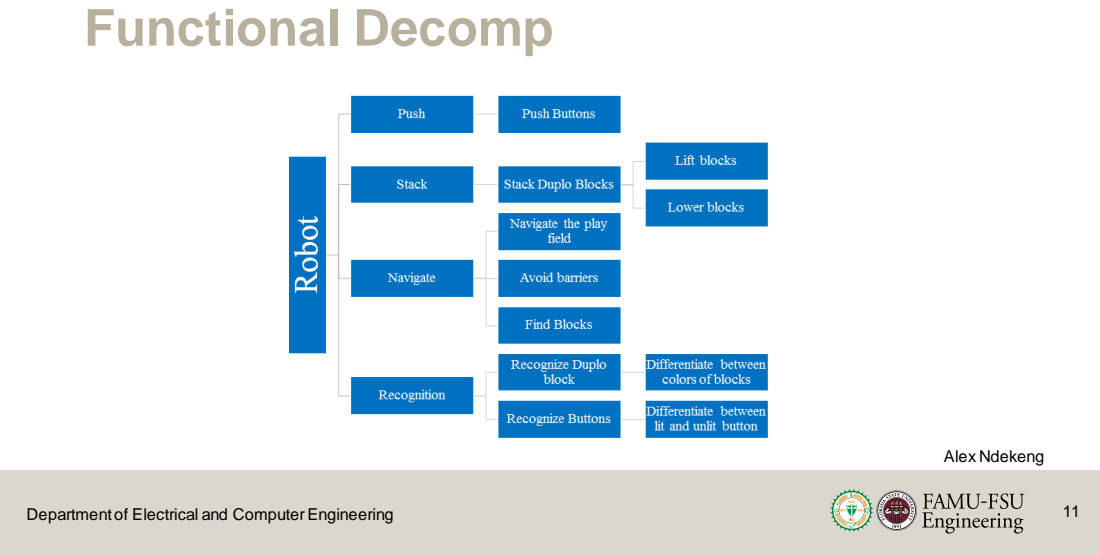
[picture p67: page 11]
Alex Ndekeng

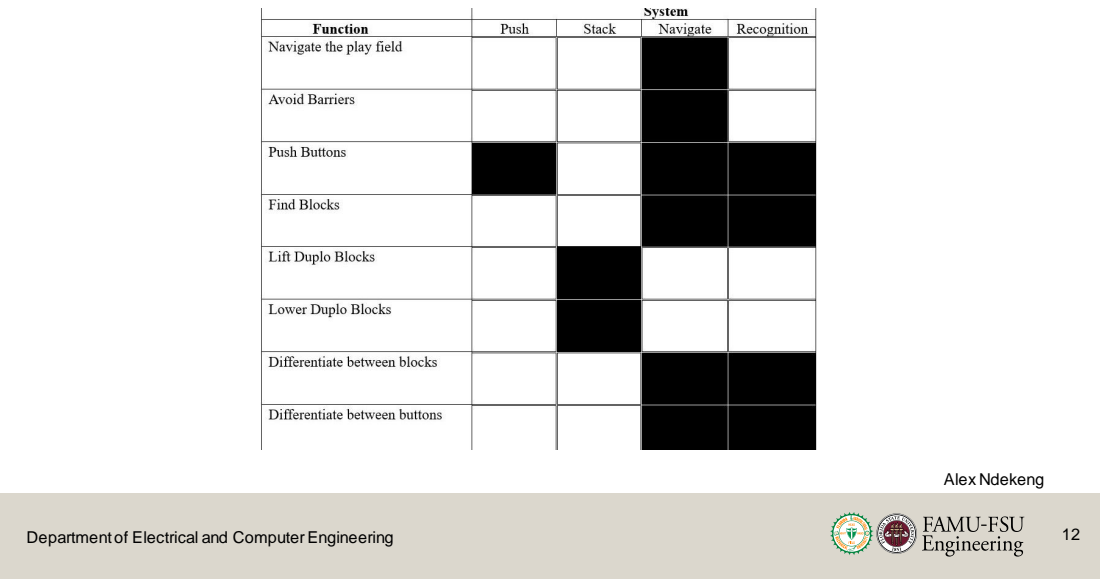
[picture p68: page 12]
Department of Electrical and Computer Engineering; Alex Ndekeng

## Connection to Systems

David Bowen

• The most important system in our product, according to the
cross-reference table is the navigation system.

• We will choose what sensors to use depending on what task we
choose to have our robot do:
• Lego Stacking
• Button Pushing

## Action and Outcome

David Bowen

• The goal of the IEEE SoutheastCon 2020 Hardware competition
is to design a robot that stacks a series of Lego Duplo blocks,
and/or inputs as many digits on a set of 10 pushbuttons in a
three-minute competition. This product will be a robot that has
all the characteristics necessary to do the challenges of the
competition.

## Thank you for your time

Contact information:; David Bowen

Team Email: southeastcon@admin.my.fsu.edu

SoutheastCon 2020 Hardware Competition

Virtual Design Review 1

## Targets and Metrics

same sensors

• Some of the measurements

will be taken through sensors

• Several functions will use the

• Navigate the play field

contains the critical target

## Validation


• The mission critical functions include to navigate the playfield,
recognize where the Duplo blocks are at, pick the Duplo blocks
and stack them correctly at the base.

• Replica arena and blocks for testing.
• Several tests will be made in order to assess the successfulness of the
design.
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

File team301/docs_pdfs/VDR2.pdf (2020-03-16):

SoutheastCon 2020 Hardware Competition

Virtual Design Review 2

Department of Electrical and Computer Engineering

# Team Introductions

Diego Campos Lead Signal Process Engineer; Isabel Barnola Lead Software Engineer; David Bowen Project Manager & Lead Robotics Engineer; Alex Ndekeng Lead Power Electronics Engineer; Abiel Souverain Lead Design Engineer

# Sponsor and Advisor

Engineering Mentor
Jerris Hooker, Ph.D.

Academic Advisor
Bruce A. Harvey, Ph.D.

Objective; Alex Ndekeng

The objective of the project is to build an autonomous robot with the
capabilities of completing at least one of the two challenges set for the 2020
SoutheastCon hardware competition.

Review; Targets and Metrics; Concepts; Final Design; Future Work; Project Background; Alex Ndekeng

## 2020 Southeast Con hardware

competition
• 1st challenge: accurately stack
Lego
Duplo blocks representing the
digits of pi.
• 2nd Challenge: push buttons
in an order that represents the
digits of pi

# Customer Needs

• We're having our customers be the same as our primary and
secondary markets as well as our stakeholders
• 12''x12''x12'' autonomous Robot
• Ability to pick up to pick up Lego blocks and stack them
• Ability to push buttons recessed in a wall
• Ability to stack Legos or push buttons in the order of the
numbers of pi
• Navigate through the arena

# Functional Decomposition

Alex Ndekeng

Targets and Metrics

Abiel Souverain & Diego Campos

# Targets and Metrics

## - Some of the measurements

same sensors; Abiel Souverain

will be taken through sensors

• Several functions will use the

• Navigate the play field

contains the critical target

# Validation

Abiel Souverain

• The mission critical functions include to navigate the playfield,
recognize where the Duplo blocks are at, pick the Duplo blocks
and stack them correctly at the base.

• Replica arena and blocks for testing.
• Several tests will be made in order to assess the successfulness of the
design.

# Validation

• Navigation: The robot will need to pass successfully different

checks such as navigating correctly to the base, and to each of

• Recognition: The robot will be assigned to go to a bin having

Duplo blocks and will need to stop once it encounters blocks at

a “pick up” distance.

# Validation

Abiel Souverain

• Pick up: The robot will have several blocks laying at a “pick up”

distance and it will need to pick them up successfully, this

implies that the robot must pick up the blocks and not let them

go unless specified.

• Stacking: A set of tests will be made to check that the robot

effectively stacks the Duplo Blocks.

# Minimum Targets

Diego Campos

1. 100 points through button pressing.

2. Score at least as many points through

stacking as through button pressing.

# Maximum Targets

1. 3380 points through correct block
stacking (13 blocks)

2. 3600 points through incorrect block
stacking (60 blocks)

3. 1500 points through button pressing

# Measurements

Diego Campos

• The “navigate the play field” function is broad and may require

some additional metrics to fully define it.

• The “avoid barriers” function will probably use the same sensors

as the “navigate the play field” function.

# Measurements

Diego Campos

• Both the “Differentiate between buttons” and the “Differentiate
between blocks” functions are measured by the time to reach
the appropriate location.

• Lifting and lowering the block will be measured by the height
difference between the current block and the previous block
placed.

Concepts; Isabel Barnola

# Challenge

# Concepts 1-2

IsabelBarnola

Robot with two arms

Scorpion
• 4 motors in the “tail.”
• Individual motors in wheels

• 2 arms to hold the Lego and stack it and has a
• Hammerlike appendage on top of one arm.

# Concepts 3-4

Robot with 2 claws and lift kit.

Color Sorting Robot
• Sorter on its body with blocks that slide in.
• Elevator and claw
• 3 DoF arm

• Two claws to raise and lower blocks.
• It will find blocks using sonar.
• Lift kit.
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

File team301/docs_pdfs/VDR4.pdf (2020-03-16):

SoutheastCon 2020 Hardware Competition

Virtual Design Review 4

Department of Electrical and Computer Engineering

# Team Introductions

Diego Campos Lead Signal Process Engineer; Isabel Barnola Lead Software Engineer; David Bowen Lead Robotics Engineer; Alex Ndekeng Lead Power Systems Engineer; Abiel Souverain Lead Design Engineer

# Sponsor and Advisor


Engineering Mentor
Jerris Hooker, Ph.D.

Academic Advisor
Bruce A. Harvey, Ph.D.

The objective of the project is to build an autonomous robot with the
capabilities of completing at least one of the two challenges set for the 2020
SoutheastCon hardware competition.

Review | Current Progress | Timeline | Future work | Summary

Project Background; Alex Ndekeng

Review | Current Progress | Timeline | Future work | Summary

# 2020 Southeast Con hardware

competition
• 1st challenge: accurately stack
Lego
Duplo blocks representing the
digits of pi.
• 2nd Challenge: push buttons
in an order that represents the
digits of pi

Review | Current Progress | Timeline | Future work | Summary

# Customer Needs

Alex Ndekeng

• We're having our customers be the same as our primary and
secondary markets as well as our stakeholders
• 12''x12''x12'' autonomous Robot
• Ability to pick up to pick up Lego blocks and stack them
• Ability to stack Legos or push buttons in the order of the
numbers of pi
• Navigate through the arena

Review | Current Progress | Timeline | Future work | Summary

# Built Practice Playfield

Review | Current Progress | Timeline | Future Work | Summary

Components; Abiel Souverain

# Ezio

# Components

`

Abiel Souverain

• Driving Motors – 99:1 gearbox
• Wheels – 80x10mm
• 6.5A Stall Current
• 1A Running Current

# Parallel Gripper

• Model is based on this gripper
from Servo City

# Components

`

Abiel Souverain; Lower Claw; Upper Claw

# Components – Laser cut bases

`

Abiel Souverain; Lower Base; Upper Base

# Components

`

Arduino Mega; Servo Motor; DC Motor Driver; Abiel Souverain

# Components – Elevator Assembly

`

• Guide Rod; Abiel Souverain

• Stepper motor with lead screw

• Geared Claw – servo controlled

Wiring Diagram; Diego Campos

# Wiring Diagram

Diego Campos

# Block Layout for 7 numbers

Diego Campos; START

# Block Layout for 10 numbers

Code; Isabel Barnola

# Pseudocode – 7 blocks

# Pseudocode – Main functions

Isabel Barnola

# Main functions What is done?

Isabel Barnola; • Stacking(); • go_to_block() • Pick(block) • drive_backwards; What is done?

• Line_following ✔
• Robot stops after line
• Velocity has to be slowed down
• IR sensors must be attached to
interrupt

• Turn ✔
• Robot turns very close to 90 degrees
• Last_stack() ✔
• Combination of turn and
line_following

# Line following - Testing

Isabel Barnola

# Line Following - Testing

`

# Programming

Isabel Barnola

# Timeline

David Bowen

# Revised Timeline

David Bowen

1. Programming – March 1, 2020
2. Functioning claw elevator – 1 week after parts arrive
3. Completed CAD – February 23, 2020
4. Fully assembled robot – Dependent on 2.
5. Competition – March 12-15, 2020

# Obstacles

• Power/Batteries
• Path Programming
• Parts being shipped
• Encoders
• Motor speed

# Parts Ordered

David Bowen

• Stepper motor with lead screw
• ABS sheets
• DC motor driver
• 12V High current battery pack
• 9V Batteries
• Hardware

# 4 Most Important Points

David Bowen

1. Discussed physical components

2. Discussed wiring and programming

3. Obstacles/revised timeline

4. Waiting on parts to arrive

Thank you for your time.

David Bowen; Review; Current Progress; Revised Timeline; Future Work

Team Email: southeastcon@admin.my.fsu.edu

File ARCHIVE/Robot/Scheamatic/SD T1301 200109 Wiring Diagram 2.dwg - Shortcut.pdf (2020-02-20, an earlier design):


Motor 1 6V DC Wheel Motor 2 6V DC Wheel 12'' MEGA ARDUINO Battery 9.6 V Battery 9.6 V Actuator Motor- Linear 6V DC 2 - Top Stall - Claw Motor 1.6 A 6V Servo 1 - Bottom Stall - Claw Motor 1.6 A 6V Servo +5v GND 6 pins Connection - Yellow Mechanical Sensors - Blue PWM - Green Ground - Grey Power - Red LEGEND: 2 pins Claw Apparatus 1 PWM pin sensor 1 pin/


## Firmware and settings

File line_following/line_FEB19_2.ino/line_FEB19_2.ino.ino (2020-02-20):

/*
  FILE :  line_following_ds_v1_0112502
  DESCRIPTION: SIMPLE LINE FOLLOWING ROBOT
  AUTHOR : ISABEL BARNOLA
  DATE: 02/05
  REFERENCES:
    https://create.arduino.cc/projecthub/robocircuits/line-follower-robot-arduino-299bae
    USING SENSOR ANALOG READ 
    EXAMPLE USES WHITE SURFACE AND THRESHOLD LINES
    TEST CURRENT SET UP AND THEN CHANGE VALUES
*/


// ================================================================
// H BRIDGE 
// ================================================================
#define ENCODEROUTPUT 4741.44
#define MIN 80
#define motor_speed 100 // MAX = 255
int motor_speed_R  = 80;//95;//85;// MAX = 255
int motor_speed_L =59;//105;//95; // MAX = 255
#define turn_speed  45
#define turn_speed1 55
#define THRESHOLD 330
#define L_Forward LOW
#define R_Forward HIGH
#define L_Backward HIGH
#define R_Backward LOW
volatile float counter_R = 0;
volatile float counter_L = 0;
unsigned int tempR;
unsigned int tempL;
float newtime;
float oldtime = 0;
unsigned int old_counter_R = 0;
unsigned int old_counter_L = 0;
float velR;
float velL;
int turn_delay = 10;
int ENC_RA = 2;
int ENC_RB = 35;
int ENC_LA = 3;
int ENC_LB = 31;
//-----------------------
// Motor : Right
//-----------------------
int R_ME  = 6;   //Enable Pin of the Right Motor (must be PWM)
int R_M1 = 51;    //Control Pin

//-----------------------
// Motor : Left
//-----------------------
int L_ME  = 4;   //Enable Pin of the Left Motor (must be PWM)
int L_M1 = 50;

int dir = 0;
int cnt = 0;

long previousMillis = 0;
long currentMillis = 0;
int interval = 1000;

// ================================================================
// IR Sensor
// ================================================================

//-----------------------
// Sensor: Left
//-----------------------

const int left_sensor_pin  = A1;
int left_sensor_state;

//-----------------------
// Sensor: Right
//-----------------------

const int right_sensor_pin = A0;
int right_sensor_state;

//-----------------------
// Sensor: Middle
//-----------------------
const int middle_sensor_pin = A2;
int middle_sensor_state;

//-----------------------
// Sensor: Left
//-----------------------

//const int left2_sensor_pin  = A3;
//int left2_sensor_state;

// ================================================================
// Function
// ================================================================

void stopp(void)                    //Stop
{
  analogWrite(R_ME,0);
  digitalWrite(R_M1,LOW);
  analogWrite(L_ME,0);
  digitalWrite(L_M1,LOW);
}
void advance(char a,char b)          //Move forward
{
  
  digitalWrite(L_M1,L_Forward);
   //delay(1);
  digitalWrite(R_M1,R_Forward);
  // delay(1);
  analogWrite (L_ME,a);  //PWM Speed Control
    //delay(1);
  analogWrite (R_ME,b);
  delay(1);
  
}
void read_ir()
{
  left_sensor_state   =  analogRead(left_sensor_pin);
  right_sensor_state  = analogRead(right_sensor_pin);
  middle_sensor_state  =  analogRead(middle_sensor_pin);
  //right2_sensor_state = analogRead(right2_sensor_pin);
   
}
void back_off (char a,char b)          //Move backward
{
  analogWrite (R_ME,a);
  digitalWrite(R_M1,R_Backward);
  analogWrite (L_ME,b);
  digitalWrite(L_M1,L_Backward);
}
void turn_L (char a,char b)             //Turn Left
{
  analogWrite (R_ME,a);
  digitalWrite(R_M1,R_Forward);
  analogWrite (L_ME,b);
  digitalWrite(L_M1,L_Backward);
}
void turn_L_line (char a)             //Turn Left
{
  analogWrite (R_ME,a);
  digitalWrite(R_M1,R_Forward);
  analogWrite (L_ME,0);
  digitalWrite(L_M1,LOW);
}
void turn_R (char a,char b)             //Turn Right
{
  analogWrite (R_ME,a);
  digitalWrite(R_M1,R_Backward);
  analogWrite (L_ME,b);
  digitalWrite(L_M1,L_Forward);
}
void turn_R_line (char b)             //Turn Right
{
  analogWrite (R_ME,0);
  digitalWrite(R_M1,LOW);
  analogWrite (L_ME,b);
  digitalWrite(L_M1,L_Forward);
}

// Motor A pulse count ISR
void ISR_countR()  
{
  //Serial.print(counter_R);
  //counter_R++;  // increment Motor A counter value
  if (digitalRead(ENC_RA) == HIGH) 
  {
    
      counter_R++;
    
  }
  if (digitalRead(ENC_LA) == HIGH) 
  {
    
      counter_L++;
  }
   
 
}
// Motor B pulse count ISR
void ISR_countL()  
{
   //Serial.print(counter_L);
  //counter_L++;  // increment Motor B counter value
  if (digitalRead(ENC_LA) == HIGH) 
  {
   
      counter_L++;
   
  }
}
void ISR_IR()
{
  left_sensor_state =  analogRead(left_sensor_pin);
  right_sensor_state = analogRead(right_sensor_pin);
  middle_sensor_state = analogRead(middle_sensor_pin);
  
  }
int count = 0;

// ================================================================
// Setup
// ================================================================

void setup() 
{
  // put your setup code here, to run once:

pinMode(ENC_RA,INPUT);
pinMode(ENC_RB,INPUT);
pinMode(ENC_LA,INPUT);
pinMode(ENC_LB,INPUT);
 
  //-----------------------
  // Motors
  //-----------------------

  // Right
  pinMode(R_M1, OUTPUT);

  // Left
  pinMode(L_M1, OUTPUT);


  //-----------------------
  // IR Sensors
  //-----------------------
  
  // Right
  pinMode(right_sensor_pin,   INPUT);
  //pinMode(right_sensor_state, INPUT);

  // Left
  pinMode(left_sensor_pin,    INPUT);
  //pinMode(right_sensor_state, OUTPUT);

  //----------------------
  // Encoders
  //----------------------

  // Increase counter A when speed sensor pin goes High
  attachInterrupt(20, ISR_countR, CHANGE);  
  //attachInterrupt(21,ISR_IR, CHANGE);
     // Increase counter B when speed sensor pin goes High
  //attachInterrupt(1, ISR_countL, CHANGE); 

  //attachInterrupt(digitalPinToInterrupt (ENC_RA), ISR_countR, RISING);  
  // Increase counter A when speed sensor pin goes High
  //attachInterrupt(digitalPinToInterrupt (ENC_LA), ISR_countL, RISING);  
  // Increase count

  //previousMillis = millis();

  // Sets the data rate in bits 
  // per second (baud) for serial data transmission.
  Serial.begin(9600); 

}
int passed = 2;
int n = 2;

  int white_lines = 0;
void loop() 
{
  
  
  /*
  Serial.println("================ NEW CODE 628 ================");
  Serial.print("previosmillis ");
  Serial.println(previousMillis);
  Serial.print("currentMillis ");
  */
  currentMillis= millis();
 // Serial.println(currentMillis);
  //-----------------------
  // IR Sensors: READ
  //-----------------------
   read_ir();
   
   Serial.print(left_sensor_state);
   Serial.print("\t");
  
   Serial.print("\t");
   //Serial.print(right2_sensor_state);
   Serial.print("\t");
   Serial.println(right_sensor_state);
  
  
  
Serial.print("-------------------------------------------------------------------White lines passed ");
Serial.println(count);
   //-----------------------
  // Navigation
  //-----------------------

  
  // RIGHT
  //      | | |  
  //       L M R
  //      | | |

  // ->
  // L(1) M(1) R(0)
  if(right_sensor_state < THRESHOLD   && middle_sensor_state < THRESHOLD && left_sensor_state > THRESHOLD) 
   //remember to check
  {
    Serial.println("turning right L(1) M(1) R(0) ");
    turn_L_line(turn_speed);
   }
    //-----------------------
    // IR Sensors: READ
    //-----------------------
     read_ir();
     
    // L(0) M(0) R(1)
   
    //      | | |  
    //       R
    //     M  | |
    //   L  | | |  

    //->
   if (right_sensor_state < THRESHOLD && middle_sensor_state > THRESHOLD && left_sensor_state > THRESHOLD)
   {
    
    Serial.println("going left L(0) M(0) R(1)");
    turn_L_line(turn_speed1);
   }

  //-----------------------
  // IR Sensors: READ
  //-----------------------
   read_ir();

  // LEFT
  //     ||||   
  //      L2||2R
  //      ||||
  // L(1) M(1) R(0)
  // <-
  if(right_sensor_state > THRESHOLD && middle_sensor_state < THRESHOLD && left_sensor_state < THRESHOLD)
  {
    Serial.println("going left");
    turn_R_line(turn_speed);
   }

  //-----------------------
  // IR Sensors: READ
  //-----------------------
   read_ir();
   
   // L(1) M(0) R(0)
   //      | | |  
   //        L  
   //      | |  M 
   //      | |    R 
   // ->
   if (right_sensor_state > THRESHOLD   && middle_sensor_state > THRESHOLD && left_sensor_state < THRESHOLD)
   {
    Serial.println("turning right L(1) M(0) R(0) ");
    turn_R_line(turn_speed1);
    }
    
  //-----------------------
  // IR Sensors: READ
  //-----------------------
   read_ir();
  
  // STOP
   if(right_sensor_state < THRESHOLD && middle_sensor_state < THRESHOLD && left_sensor_state < THRESHOLD){
     if (white_lines == n)
     {
        Serial.println("stop");
        stopp();
     }
     else
     {
      while(right_sensor_state < THRESHOLD && left_sensor_state < THRESHOLD && middle_sensor_state < THRESHOLD)
      {
          read_ir();
         Serial.print("|||||||||||||||| PASSING WHITE||||||||||||||||||  ");
         Serial.println(white_lines);
        advance(motor_speed_R,motor_speed_L);
        Serial.print("=====================================================right_sensor_state ");
        Serial.println(right_sensor_state);
        Serial.print("=====================================================left_sensor_state");
        Serial.println(left_sensor_state);

     /* Serial.print("===================counL: ");
    Serial.println(counter_L);
    Serial.print("=====================counR: ");
    Serial.println(counter_R);
    */
  
    velR = counter_R /(currentMillis - previousMillis);
    velL = counter_L /(currentMillis - previousMillis);
    /*
    Serial.print("===============================velR: ");
    Serial.println(velR);
    Serial.print("===============================velL: ");
    Serial.println(velL);
    */

      if (velR > velL && motor_speed_R > MIN && motor_speed_L> MIN)
      {
         motor_speed_L--;
        //Serial.println("--------------------changing left");
        
       
      }
      else if (velL >  velR && motor_speed_R > MIN && motor_speed_L> MIN)
      {
       motor_speed_R--;
        //Serial.println("--------------------changing right");
        
      }
      
       /*
        Serial.print("Right speed:");
        Serial.println( motor_speed_R);
         Serial.print("left speed:");
        Serial.println(motor_speed_L);
  */
        cnt++;
       
        counter_R = 0;
        counter_L = 0;
        
    
     
      }
      white_lines++;
      count++;
      Serial.print("-------------------------------------lines passed: ");
      Serial.println(white_lines);
     }
     
    
  }

  //-----------------------
  // IR Sensors: READ
  //-----------------------
   read_ir();

  // FORWARD
  if(right_sensor_state > THRESHOLD && left_sensor_state > THRESHOLD && middle_sensor_state)
  
  {
    if (dir != 1)
    {
       dir = 1;
       cnt = 0;
    }

    Serial.println("going forward");
    advance(motor_speed_R,motor_speed_L);

    /*  Serial.print("===================counL: ");
    Serial.println(counter_L);
    Serial.print("=====================counR: ");
    Serial.println(counter_R);
  */
    velR = counter_R /(currentMillis - previousMillis);
    velL = counter_L /(currentMillis - previousMillis);
    /*
    Serial.print("===============================velR: ");
    Serial.println(velR);
    Serial.print("===============================velL: ");
    Serial.println(velL);
*/
      if (velR > velL && motor_speed_R > MIN && motor_speed_L> MIN)
      {
         motor_speed_L--;
        //Serial.println("--------------------changing left");
        
       
      }
      else if (velL >  velR && motor_speed_R > MIN && motor_speed_L> MIN)
      {
       motor_speed_R--;
       // Serial.println("--------------------changing right");
        
      }
      
       /*
        Serial.print("Right speed:");
        Serial.println( motor_speed_R);
         Serial.print("left speed:");
        Serial.println(motor_speed_L);
  */
        cnt++;
       
        counter_R = 0;
        counter_L = 0;
        
    
     
  
   
  }
   previousMillis = currentMillis;
  //delay(500);
}

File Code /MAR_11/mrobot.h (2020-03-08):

            /*function prototypes */
            
            void pwm_init(void);             /*initialize pwm*/
            void direction_init(void);       /*initialize direction pins*/
            
            void pwm_set_duty(int channel, int duty);
            void set_direction(int channel, int dir);
            
            void motor_init(void);          /* call pwm_init and direction_init */ 
            void set_motor_duty(int channel, int duty); 
            
            void setup_timer(void); 
            void get_current_status(void);
            
            void ADC_init(void);           /*initiliaze analog to digital for IR sensor*/
            int ADC_read(uint8_t channel); /* read analog channel 
                                          /* channel = 0 for A0 - right sensor 
                                             channel = 1 for A1 - front sensor 
                                             channel = 2 for A2 - left sensor*/
            

      

            #define PI 3.1416

            /****** Motor Function ******/
 
            
            void motor_init(void)
            {
              pwm_init();
              direction_init();
            }
            
            void set_motor_speed(int channel, int duty)
            {
                pwm_set_duty(channel,duty);
            }
            
            void direction_init(void){
                pinMode(50,OUTPUT); //motor right enable
                pinMode(51,OUTPUT); //motor left enable
                
            } /*end of direction_init*/
            
            
            void pwm_init(void){//pwm set up
                pinMode(4, OUTPUT); //motor 0
                pinMode(6, OUTPUT); //motor 1
                TCCR5A = _BV(COM5A1) | _BV(COM5B1) | _BV(WGM52) | _BV(WGM50);
                TCCR5B = _BV(CS51) | _BV(CS50);  //set prescaler to 128
                OCR5A  =  0;
                OCR5B  =  0;
            } /*end of pwm_init*/
            
            
            
            void pwm_set_duty(int channel, int duty)
            { 
               
                if (duty > 255){ 
                  duty = 255;
                  }
                  else if(duty < -255){
                  duty = -255;
                  }
            
                  
                  if (duty>0) {
                  set_direction(channel,1);      // forward 
                  }
                  else if(duty<0) {
                    set_direction(channel, 0);   //reverse
                    duty = -duty;
                    }
                    
                 if (channel==0)  //motor 0 (left motor)
                    OCR5B = duty; //pin45
                    
                 else if (channel ==1)//motor 1(right motor)
                    OCR5A = duty; //pin46
            }
            /*end of pwn_set_duty*/
            
            
            void set_direction(int channel, int dir)//set motor direction
            {
                if (channel == 1)//motor 1(right)
                 {
                  if(dir == 0) //reverse 
                   {
                    digitalWrite(50,HIGH);  //I3
                    digitalWrite(51,HIGH); //I4
                    }
                   else if(dir == 1) //forward
                   {
                    digitalWrite(50,LOW); //I3
                    digitalWrite(51,LOW);  //I4
                    }
                    
                  } /*end if channel ==1 */
                  
                 else if(channel == 0) //motor 1(left)
                 {
                  if(dir == 0) //reverse
                   {
                    digitalWrite(50,LOW);  //I1
                    digitalWrite(51,HIGH); //I2
                    }
                   else if(dir == 1) //forward
                   {
                    digitalWrite(50,HIGH); //I1
                    digitalWrite(51,LOW);  //I2
                   }
                 }  /*end else if */
            } /*end set_direction*/
            
            
            /****************************  Encoder Functions  *********************************/ 




          void encoder_init(void);
          void encoder0CHB(void);
          void encoder0CHA(void);
          void encoder1CHB(void);
          void encoder1CHA(void);

          const byte interruptPIN2 = 24;//26;//24; // YELLOW RIGHT
          const byte interruptPIN3 = 25;//27;//25; // WHITE  RIGHT
          const byte interruptPIN0 = 26;//24;//26; // YELLOW LEFT
          const byte interruptPIN1 = 27;//25;//27; // WHITE  LEFT

          byte state0 = 0;
          byte state1 = 0;
          
          long int encoder0_val=0;
          long int encoder1_val=0;

          void encoder_init(void){
            
                  pinMode(interruptPIN2, INPUT_PULLUP);
                  pinMode(interruptPIN3, INPUT_PULLUP);
                  attachInterrupt(digitalPinToInterrupt(interruptPIN2), encoder0CHA, CHANGE);//set GPIO pin for encoder
                  attachInterrupt(digitalPinToInterrupt(interruptPIN3), encoder0CHB, CHANGE);//set GPIO pin for encoder


                  
                  pinMode(interruptPIN0, INPUT_PULLUP);
                  pinMode(interruptPIN1, INPUT_PULLUP);
                  attachInterrupt(digitalPinToInterrupt(interruptPIN0), encoder1CHA, CHANGE);//set  GPIO pin for encoder
                  attachInterrupt(digitalPinToInterrupt(interruptPIN1), encoder1CHB, CHANGE);//set  GPIO pin for encoder
          }


        /******* Encoder 0 for Motor 0 ************************/
          
        void encoder0CHA(void) //function to read and determine state of encoder 0-A
          {
              if ((state0 == 0) && (digitalRead(interruptPIN2) ==1))
                    {
                          state0 =1;
                          encoder0_val +=1;
                    }
              else if ((state0==1) && (digitalRead(interruptPIN2) ==0))
                    {
                          state0 =0;
                          encoder0_val -=1;
                    }
               else if ((state0==2) && (digitalRead(interruptPIN2) ==1))
                    {
                          state0 =3;
                          encoder0_val -=1;
                    }
              else if ((state0==3) && (digitalRead(interruptPIN2) ==0))
                   {
                          state0 =2;
                          encoder0_val +=1;
                    }
            }
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

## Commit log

2020-02-20 Last for FEB 19
    [ROBOT.fzz]
2020-02-20 correction with dr. chuy's code
    [line_FEB20.ino.ino, mrobot.h]
